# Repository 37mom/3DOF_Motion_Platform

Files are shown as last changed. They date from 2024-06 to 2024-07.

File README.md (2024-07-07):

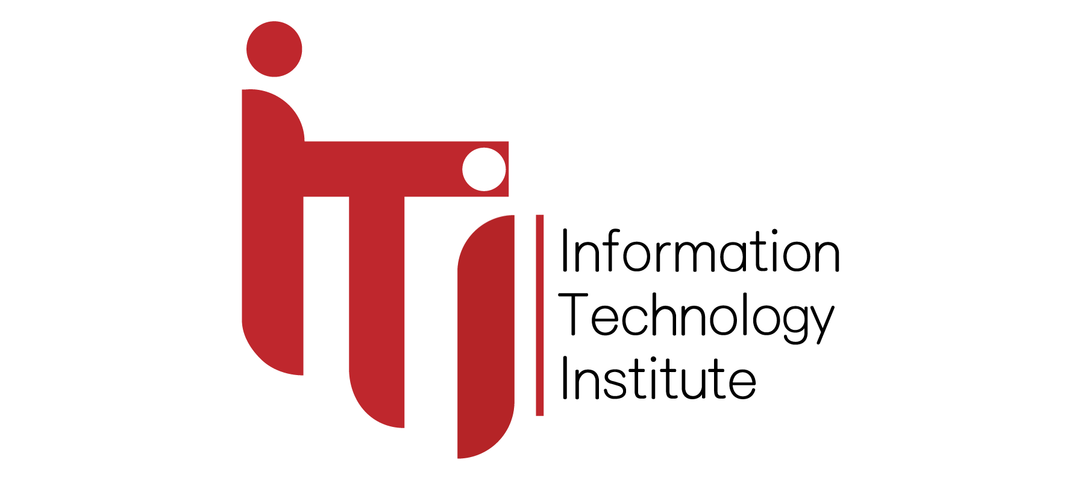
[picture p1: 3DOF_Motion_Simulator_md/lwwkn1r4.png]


> Information Technology Institute
>
> Motion Simulator
>
> Robotics
>
> Israa Ahmed Merhan Wael Mohamed Omar
>
> Submitted to Eng. Omar Shehata
>
> May 9, 2018
>
> Contents
>
> 1 Introduction 2
>
> 2 Robot Kinematics 3
>
> 3 Kinematics Of 3-DOF Parallel Robot 5 3.1 Forward Position Kinematics
> . . . . . . . . . . . . . . . . . . . 5 3.1.1 Vector loop equations: .
> . . . . . . . . . . . . . . . . . 5
>
> 3.1.2 Rotation Matrices . . . . . . . . . . . . . . . . . . . . . 5
> 3.1.3 EE Position Equations . . . . . . . . . . . . . . . . . . 8
> 3.1.4 Constrain Equations . . . . . . . . . . . . . . . . . . . 8
>
> 3.2 Solid-Work Model Veriﬁcation . . . . . . . . . . . . . . . . . . 9
> 3.3 Inverse Position Kinematics . . . . . . . . . . . . . . . . . . .
> 10 3.3.1 Orientation Equations . . . . . . . . . . . . . . . . . . 10
> 3.3.2 Passive angle equations . . . . . . . . . . . . . . . . . . 11
> 3.3.3 Position Equations . . . . . . . . . . . . . . . . . . . . 11
>
> 4 Forward Velocity Kinematics 12
>
> 5 Inverse Velocity Kinematics 13 5.1 Constrain equations
> diﬀerentiation . . . . . . . . . . . . . . . 13 5.2 EE position
> equations diﬀerentiation . . . . . . . . . . . . . . 13
>
> 6 Simulation 14 6.1 Trajectory Planning . . . . . . . . . . . . . . .
> . . . . . . . . 14 6.1.1 Circular Trajectory . . . . . . . . . . . . .
> . . . . . . . 15
>
> 6.1.2 Rectangular Trajectory . . . . . . . . . . . . . . . . . . 16
>
> 7 References 17
>
> 1

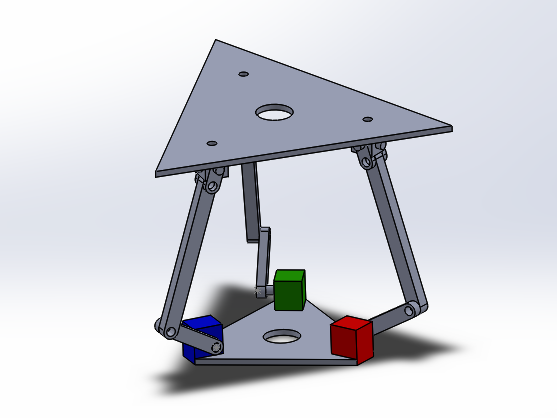
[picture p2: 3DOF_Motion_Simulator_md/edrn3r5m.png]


> 1 Introduction
>
> This project aims to design and manufacture a 3-DOF motion simulator
> plat-form. It is divided into three main parts : modelling, mechanical
> design and control.
>
> Motion simulators are used to simulate virtual motion into real life,
> for exam-ple they are used in ﬂight and car simulators to test
> aircrafts or cars or even to practice ﬂying an airplane before being
> in an actual one. Another usage of motion simulators which is the
> topic of this project is game simulation, for example imagine that you
> play a car-racing game while sitting on this platform you will
> experience the feeling of being inside the game.
>
> Figure 1: Solidworks model
>
> 2

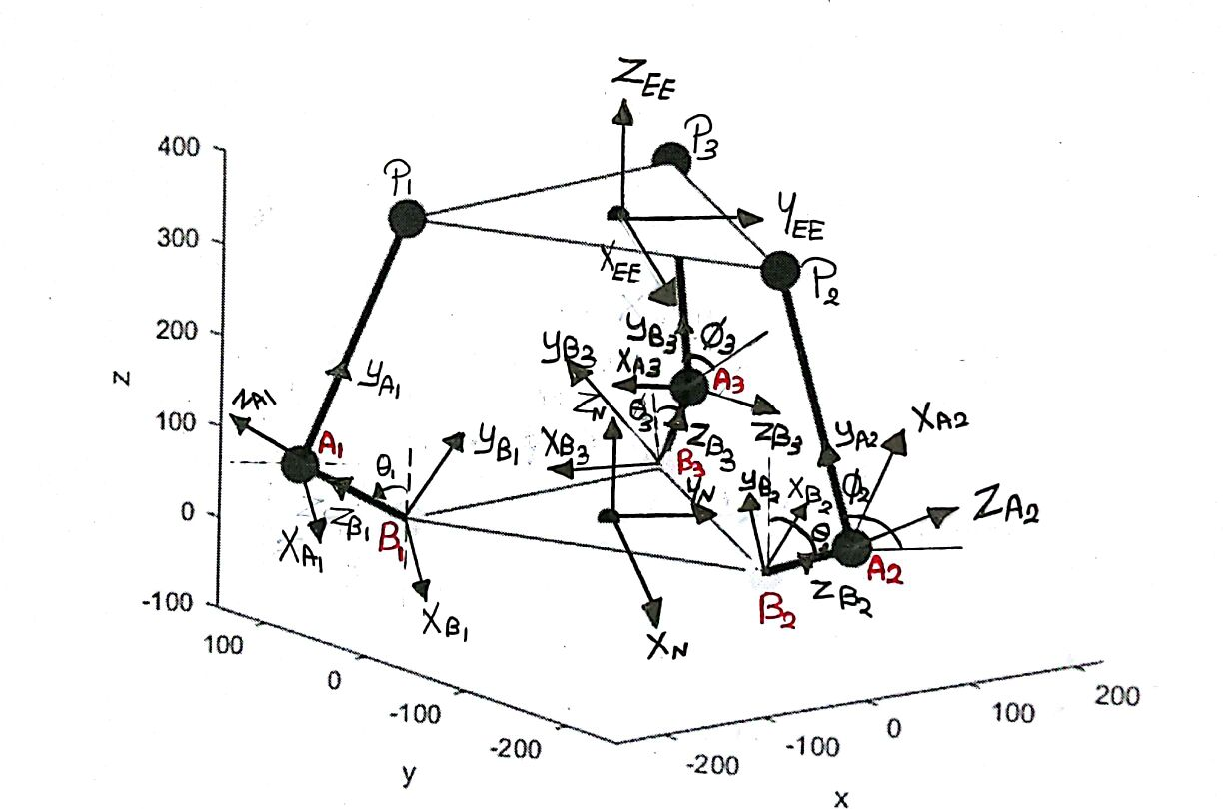
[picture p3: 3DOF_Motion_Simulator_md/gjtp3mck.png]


> 2 Robot Kinematics
>
> Our motion simulator can be described as a parallel manipulator with
> 3-DOF, two rotational motions (roll and pitch) and one translational
> motion in direction of Z-axis. The robot consists of 3 legs connected
> together through a platform, each leg consists of 2 links connected
> together through a revolute joint, each leg is connected to a motor
> through a revolute joint and to the platform through a U-joint.
>
> The kinematics problem of parallel manipulators is very tedious so we
> de-cided to simplify our problem by treating this robot as 3 serial
> robotic arms connected together through the platform which will be the
> work space of our robot, these ﬁxation points are ﬁxed in position
> forming an equilateral triangle and ﬁnally we neglected the presence
> of the U-joint but added the orientation of platform to our
> calculations. The motor axes of rotation are ﬁxed at 120 rotated from
> each other creating an equilateral triangle.
>
> Setting 2 coordinate systems for each link and the base frame. In the
> median of the base triangle the Newtonian frame XNYNZN is selected and
> this is the ﬁxed coordinate system. Z-axis in the ﬁxed frame is
> vertically
>
> 3
>
> upwards, X-axes of the frames at motor points are co-linear with the
> axes of rotation of the motors and the x-axis of the Newtonian frame
> is parallel to the axis of the ﬁrst coordinate system of the ﬁrst
> motor(B1). 0s are the 3 active angles of our system created by
> rotating about (Xi) and it is between the vertical axis of the base
> frame (ZN) and (ZBi) (ZB1 is coincident with
>
> the link BiAi) . is are the 3 passive angles created by rotating about
> (Xi) and they are measured between (YN) and (YAi) (YAi is coincident
> with the link AiPi).
>
> 4
>
> 3 Kinematics Of 3-DOF Parallel Robot
>
> 3.1 Forward Position Kinematics 3.1.1 Vector loop equations:
>
> Link(1):
>
> Link(2):
>
> Link(3):
>
> jrOE = -ljYN +l1jZB1 +l2jYA1 (1)

jrOE = ljXN + 2 l 3jYN +l1jZB2 +l2jYA2 (2)

> rOE = -ljXN + 2 l 3jYN +l1jZB3 +l2jYA3 (3)
>
> 3.1.2 Rotation Matrices
>
> Link(1):
>
> 2 1 0 NRB1 = 4 0 cos1
>
> 0 sin1

0 3 -sin1 5,

> cos1

2 1 0 NRA1 = 4 0 cos1

> 0 sin1

0 3 -sin1 5

> cos1
>
> 5
>
> Link(2):
>
> 2 cos -sin 0 3 NRB21 = 4 cos -sin 0 5,
>
> 0 0 1
>
> 1 0 0 A21RA2 = 4 0 cos2 -sin2 5,
>
> 0 sin2 cos2
>
> cos -cos2 sin sin2 sin NRB2 = sin cos2 cos -sin2 cos
>
> 1 0 0
>
> cos -cos2 sin sin2 sin NRA2 = sin cos2 cos -sin2 cos
>
> 1 0 0
>
> 2 1 0 B21RB2 = 4 0 cos2
>
> 0 sin2
>
> NRA21 = NRB21

3

5

> 3
>
> 5

0 3 -sin2 5

> cos2
>
> Link(3):
>
> 2 cos2 -sin2 0 3 NRB31 = 4 cos2 -sin2 0 5,
>
> 0 0 1
>
> 1 0 0 A31RA3 = 4 0 cos3 -sin3 5,
>
> 0 sin3 cos3
>
> cos2 -cos3 sin2 sin3 sin2 NRB3 = sin2 cos3 cos2 -sin3 cos2
>
> 1 0 0
>
> cos2 -cos3 sin2 sin3 sin2 NRA3 = sin2 cos3 cos2 -sin3 cos2
>
> 1 0 0
>
> 2 1 0 B31RB3 = 4 0 cos3
>
> 0 sin3
>
> NRA31 = NRB31

3

5

> 3
>
> 5

0 3 -sin3 5

> cos3
>
> 6
>
> Link 1: Where :
>
> ZB1 = -sin1jYN +cos1jZN (4) YA1 = cos1jYN +sin1jZN (5)
>
> Final Calculations:
>
> XP1 = 0
>
> YP1 = <u>-l</u> -l1 sin1 +l2 cos1
>
> ZP1 = l1 cos1 +l2 sin1
>
> Link 2: Where :
>
> ZB2 = sin sin2jXN -cos sin2jYN +cos2jZN (6) YA2 = sin sin2jXN
> -cossin2jYN +cos2jZN (7)
>
> Final Calculations:
>
> XP2 = <u>l</u> +l1 sin sin2 -l2 cos2 sin
>
> YP2 = 2 <u>l</u> 3 -l1 sin2 cos +l2 cos2 cos ZP2 = l1 cos2 +l2 sin2
>
> Link 3: Where :
>
> ZB3 = sin(2 )sin3jXN -cos(2 )sin3jYN +cos3jZN (8) YA3 = -sin(2
> )cos3jXN -cos(2 )cos3jYN +cos3jZN (9)
>
> 7
>
> Final Calculations:
>
> XP3 = <u>-l</u> +l1 sin(2 )sin3 -l2 cos3 sin(2 )
>
> YP3 = 2 <u>l</u> 3 -l1 sin3 cos(2 )+l2 cos3 cos(2 ) ZP2 = l1 cos3 +l2
> sin3
>
> 3.1.3 EE Position Equations
>
> The EE point is the median of the triangle connecting the 3-edges of
> the 3-Links.
>
> XEE = Xp1 +Xp2 +Xp3 (10)
>
> YEE = Yp1 +Yp2 +Yp3 (11)
>
> ZEE = Zp1 +Zp2 +Zp3 (12)
>
> 3.1.4 Constrain Equations
>
> The constrain Equation of this robot is that any distance between any
> two edges is constant and it is equal to the length of the triangle
> that connects the 3-edges.
>
> So the constrain equations are :
>
> ~~q~~
>
> C1 = (Xp1 -Xp2)2 +(Yp1 -Yp2)2 +(Zp1 -Zp2)2 (13)
>
> ~~q~~
>
> C2 = (Xp1 -Xp3)2 +(Yp1 -Yp3)2 +(Zp1 -Zp3)2 (14)
>
> ~~q~~
>
> C3 = (Xp3 -Xp2)2 +(Yp3 -Yp2)2 +(Zp3 -Zp2)2 (15)
>
> Where
>
> C1 = C2 = C3 = d (16)
>
> Where d is the length of the triangle.
>
> By solving the 3-previous equations using Newton Raphson , the passive
> angles 0s can be obtained.
>
> Applying 0s and 0s in the Vector Loop equations , the positions of the
> 3-edges and EE can be obtained.
>
> 8
>
> 3.2 Solid-Work Model Veriﬁcation
>
> Comparsion

||
||
||

||
||
||

||
||
||

||
||
||

82 76.63 82.8 80.63 77.47 83.746

||
||
||

||
||
||

||
||
||

88.86 88.86 88.69 90.85 90.85 90.85

||
||
||

||
||
||

||
||
||

68.244 68.244 68.244 69.98 69.98 69.98

||
||
||

||
||
||

||
||
||

69.45 84.32 74.63 69.76 85.73 75.78

||
||
||

> Table 1: Model Veriﬁcation
>
> 9
>
> 3.3 Inverse Position Kinematics 3.3.1 Orientation Equations
>
> Due to the platform orientation around x-axis and y-axis (Pitch and
> Roll) , the position of 3-edges of the triangle can be obtained as a
> function in the EE position and the platform orientation ( and ).
>
> is the angle due to the orientation around x-axis of the ﬁxed frame.
>
> is the angle due to the orientation around y-axis of the ﬁxed frame.
>
> 10
>
> 3.3.2 Passive angle equations
>
> Zpi = f(,) (17)
>
> The previous equation shows that 0s function in 0s and Zpi. So the
> equations will be:
>
> Link(1):
>
> Link(2):
>
> Link(3):

1 = sin-1(Zp1 -l1cos(1)) (18) 2

2 = sin-1(Zp2 -l1cos(2)) (19) 2

3 = sin-1(Zp3 -l1cos(3)) (20) 2

> 3.3.3 Position Equations
>
> -l -l1 sin1 +l2 cos1 -YP1 = 0 (21)
>
> 2 l 3 -l1 sin2 cos +l2 cos2 cos -YP2 = 0 (22) 2 l 3 -l1 sin3 cos(2
> )+l2 cos3 cos(2 )-YP3 = 0 (23)
>
> by substituting equations 18,19,20 in equations 21,22,23 ,we can get
> the 0s and 0s.
>
> 11
>
> 4 Forward Velocity Kinematics
>
> In order to solve the velocity kinematics problem, the velocity of the
> end eﬀector must be found using the angular speed of the motors as the
> input. After diﬀerentiating the constraint equations using the
> following equations :
>
> @C1 @C1 @i @C1 @i @t @i @t @i @t
>
> @C2 @C2 @i @C2 @i @t @i @t @i @t @C3 @C3 @i @C3 @i
>
> @t @i @t @i @t

\(24\)

\(25\)

\(26\)

> Now these equations become 3 linear equations in 0s (passive angles’
> angular velocities) because in these equations the end eﬀector
> position, mo-tor angles and passive angles are givens to these
> equations , by solving them together we obtain 0s . Now it’s necessary
> to diﬀerentiate the end eﬀector position equations for each link in
> order to obtain the velocity of the end eﬀector of the whole platform.
>
> As,
>
> XEE = Xp1 +Xp2 +Xp3 (27)
>
> YEE = Yp1 +Yp2 +Yp3 (28)
>
> ZEE = Zp1 +Zp2 +Zp3 (29)
>
> 12
>
> 5 Inverse Velocity Kinematics
>
> The inverse velocity kinematic problem can be solved by getting the
> values of angular velocity (i).
>
> By diﬀerentiating the EE position equations and the constrain
> equations w.r.t and .
>
> 5.1 Constrain equations diﬀerentiation
>
> @C1 @C1 @i @C1 @i @t @i @t @i @t @C2 @C2 @i @C2 @i @t @i @t @i @t @C3
> @C3 @i @C3 @i @t @i @t @i @t
>
> 5.2 EE position equations diﬀerentiation

\(30\)

\(31\)

\(32\)

> @XEE 1 @(Xp1 +Xp2 +Xp3)@i @(Xp1 +Xp2 +Xp3)@i @t 3 @i @t @i @t
>
> @YEE 1 @(Yp1 +Yp2 +Yp3)@i @(Yp1 +Yp2 +Yp3)@i @t 3 @i @t @i @t
>
> @ZEE 1 @(Zp1 +Zp2 +Zp3)@i @(Zp1 +Zp2 +Zp3)@i @t 3 @i @t @i @t

\(33\)

\(34\)

\(35\)

> Where XEE , YEE and ZEE are the input to the inverse velocity
> kinematic problem . So, by solving this 6-equations using fsolve
> function , i and i can be obtained.
>
> 13
>
> 6 Simulation
>
> 6.1 Trajectory Planning
>
> In this section it is supposed to simulate the motion of a ball on the
> plat-form using the robot kinematics. In order to simulate the ball
> motion, the diﬀerential equations describing the ball motion is added
> to the rest of the system’s equation.
>
> a1 dtx + dt a2 +a3 dt+xdt 2 = -gsin (36)
>
> 2 2
>
> a1 dt2 + dt a2 +a3 dt +y dt = -gsin (37)
>
> As,
>
> a1 = 1+ mb(rb)2 a2 = mbrb
>
> Where,

a3 = Kcx b

> mb is the ball mass.
>
> rb is the ball radius.
>
> Jb is the moment of inertia of the ball.
>
> Kb is the coeﬃcient of friction of the ball.
>
> By changing the orientation of the platform (by changing values of & )
> with respect to time in order to set a rectangular and a circular
> trajectories for the ball then solving the previous equations for
> these inputs to specify the position of the ball on the plate.
>
> 14

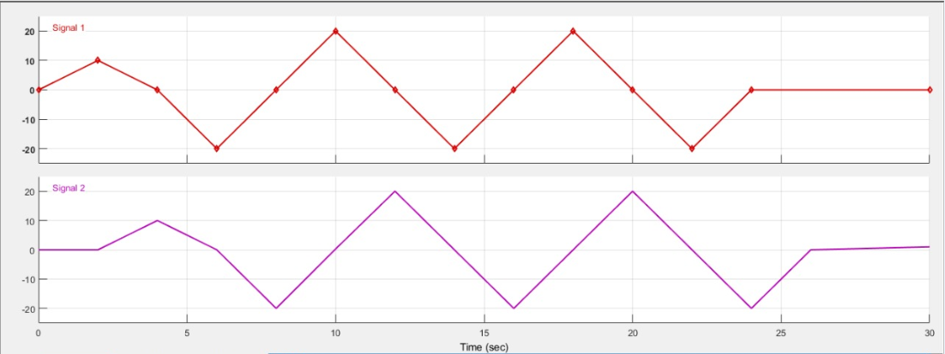
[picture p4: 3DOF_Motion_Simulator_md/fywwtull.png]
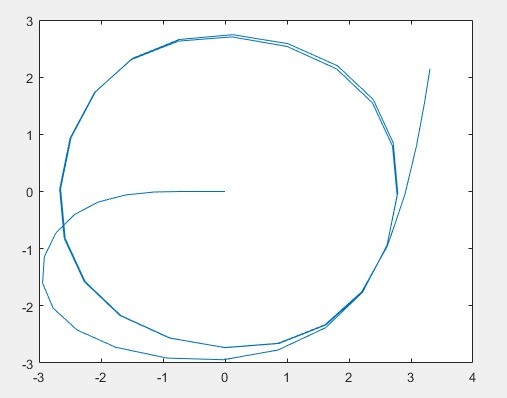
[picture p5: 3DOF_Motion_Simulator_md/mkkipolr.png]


> 6.1.1 Circular Trajectory
>
> System Input Signal:
>
> Figure 2: Orientation angles input
>
> Path:
>
> Figure 3: Circular trajectory
>
> 15

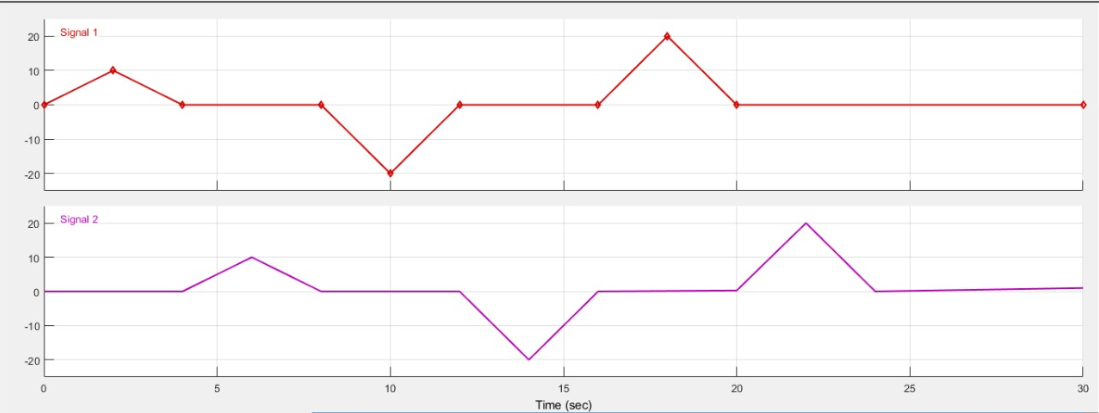
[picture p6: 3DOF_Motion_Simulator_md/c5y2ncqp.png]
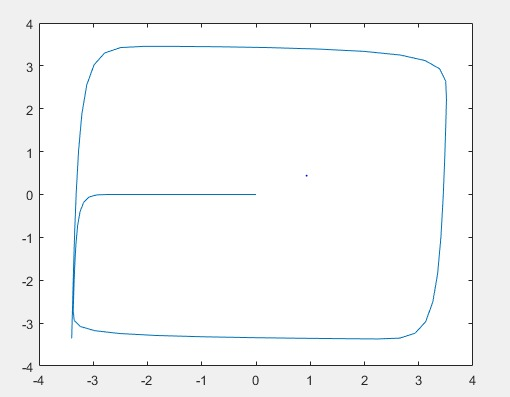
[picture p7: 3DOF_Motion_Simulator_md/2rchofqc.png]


> 6.1.2 Rectangular Trajectory
>
> System Input Signal:
>
> Figure 4: Orientation angles input
>
> Path:
>
> Figure 5: Rectangle trajectory
>
> 16
>
> 7 References
>
> 1\. An Upper Limb Rehabilitation Robot Based on 3-RRC Parallel
> Mech-anism Hongbo Wang, Ning Du, Huina Hou, Jiangshun Zhao and
> Hong-nian Yu,Proceedings of the 2012 International Conference on
> Advanced Mechatronic Systems, Tokyo, Japan, September 18-21,2012.
>
> 2\. Kinematics and dynamics analysis of a three degree-of-freedom
> paral-lel manipulator LIU Shan-zeng, ZHU Zhen-cai, SUN Zhao-peng, CAO
> Guo-hua School of Mechanical and Electrical Engineering, China
> Uni-versity of Mining and Technology, Xuzhou 221116, China Central
> South University Press and Springer-Verlag Berlin Heidelberg 2014,J.
> Cent. South Univ. (2014).
>
> 3\. Modelling of Ball and Plate System Based on First Principle Model
> and Optimal Control František Dušek, Daniel Honc, Rahul Sharma K.
> Department of Process Control, Faculty of Electrical Engineering and
> Informatics University of Pardubice nám. Čs. legií 565, 532 10
> Par-dubice, Czech Republic frantisek.dusek@upce.cz,
> daniel.honc@upce.cz, rahul.sharma@student.upce.cz, 2017 21st
> International Conference on Process Control (PC) June 6–9, 2017,
> Štrbské Pleso, Slovakia.
>
> 17

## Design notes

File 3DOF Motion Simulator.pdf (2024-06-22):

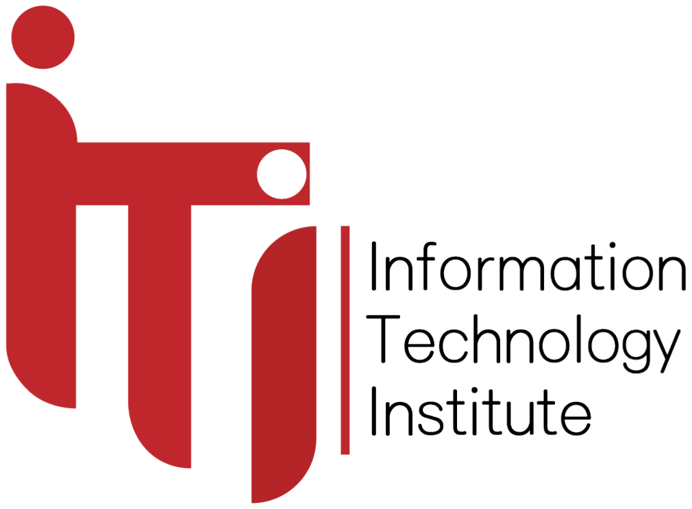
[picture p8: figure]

Information Technology Institute

Motion Simulator

# Robotics

## Israa Ahmed Merhan Wael Mohamed Omar

Submitted to
Eng. Omar Shehata

### May 9, 2018

## Contents

1 Introduction | 2
2 Robot Kinematics | 3
3 Kinematics Of 3-DOF Parallel Robot | 5
4 Forward Velocity Kinematics | 12
5 Inverse Velocity Kinematics | 13
6 Simulation | 14
7 References | 17

1

## 1 Introduction

This project aims to design and manufacture a 3-DOF motion simulator platform. It is divided into three main parts : modelling, mechanical design and control.
Motion simulators are used to simulate virtual motion into real life, for example they are used in flight and car simulators to test aircrafts or cars or even to practice flying an airplane before being in an actual one. Another usage of motion simulators which is the topic of this project is game simulation, for example imagine that you play a car-racing game while sitting on this platform you will experience the feeling of being inside the game.

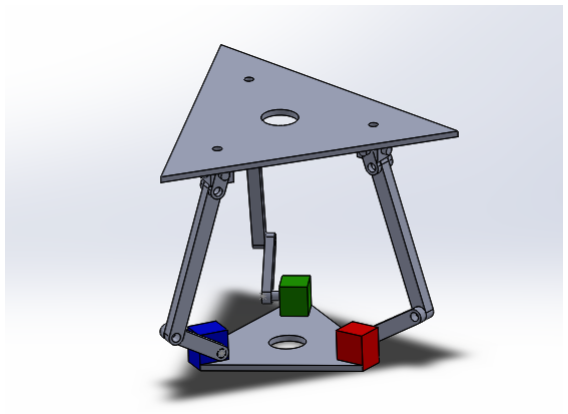
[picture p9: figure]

Figure 1: Solidworks model

2

## 2 Robot Kinematics

Our motion simulator can be described as a parallel manipulator with 3-DOF, two rotational motions (roll and pitch) and one translational motion in direction of Z-axis. The robot consists of 3 legs connected together through a platform, each leg consists of 2 links connected together through a revolute joint, each leg is connected to a motor through a revolute joint and to the platform through a U-joint.

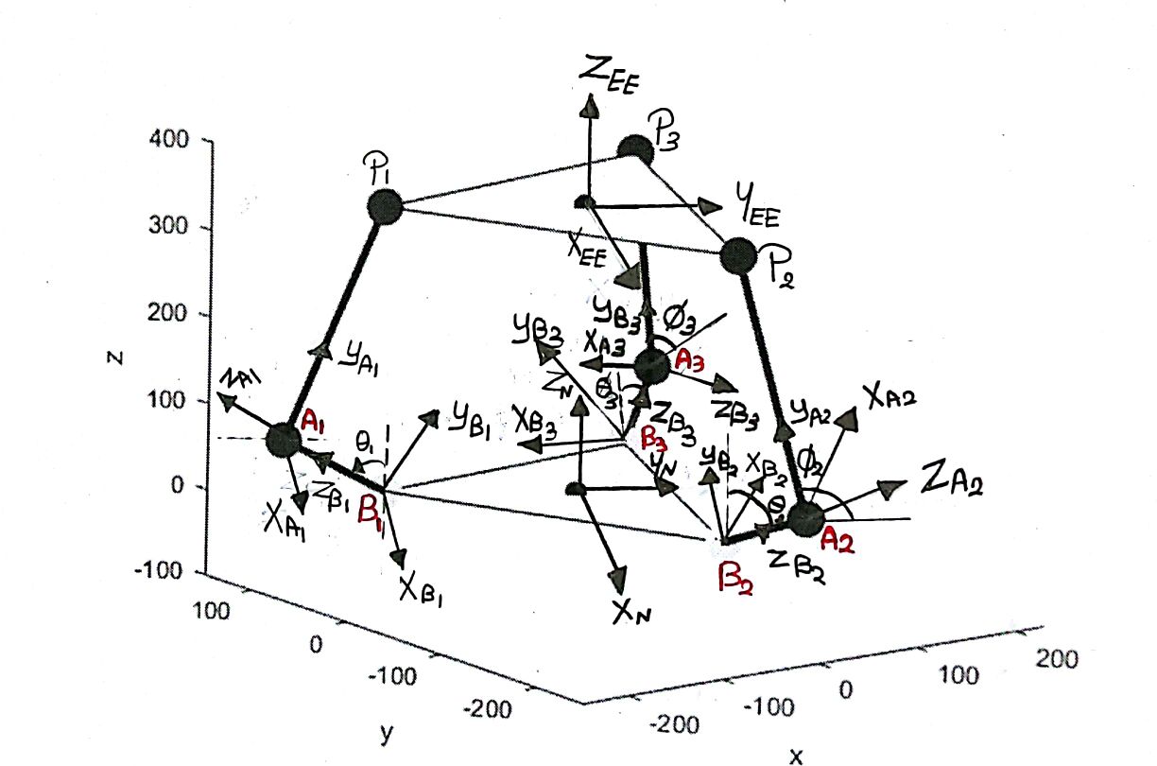
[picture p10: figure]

The kinematics problem of parallel manipulators is very tedious so we de-cided to simplify our problem by treating this robot as 3 serial robotic arms connected together through the platform which will be the work space of our robot, these fixation points are fixed in position forming an equilateral triangle and finally we neglected the presence of the U-joint but added the orientation of platform to our calculations. The motor axes of rotation are fixed at 120◦
rotated from each other creating an equilateral triangle.

Setting 2 coordinate systems for each link and the base frame. In the median of the base triangle the Newtonian frame XNYNZN is selected and this is the fixed coordinate system. Z-axis in the fixed frame is vertically

3

upwards, X-axes of the frames at motor points are co-linear with the axes of rotation of the motors and the x-axis of the Newtonian frame is parallel to the axis of the first coordinate system of the first motor(B1). θ

0
i

s are the 3
active angles of our system created by rotating about (Xi) and it is between the vertical axis of the base frame (ZN) and (ZBi

) (ZB1
is coincident with
the link BiAi) . φ⁰
i

s are the 3 passive angles created by rotating about (Xi) and they are measured between (YN) and (YAi

) (YAi
is coincident with the
link AiPi).

4

## 3 Kinematics Of 3-DOF Parallel Robot

### 3.1 Forward Position Kinematics

### 3.1.1 Vector loop equations:

- Link(1):

|r

OE =

−l
√
3
|YN + l1|ZB1 + l2|YA1 | (1)
- Link(2):

|r

OE =

l
2

|XN +

l
2

√
3
|YN + l1|ZB2 + l2|YA2 | (2)
- Link(3):

r

OE =

−l
√
3

|XN +

l
2

√
3
|YN + l1|ZB3 + l2|YA3 | (3)

### 3.1.2 Rotation Matrices

- Link(1):

NRB1 =

1 | 0 | 0
0 cos θ1 | − sin θ1
0 sin θ1 | cos θ1
- ,

NRA1 =

1 | 0 | 0
0 cos φ1 | − sin φ1
0 sin φ1 | cos φ1

5

- Link(2):

NRB21 =

cos ψ − sin ψ 0
cos ψ − sin ψ 0
0 | 0 | 1
- ,

B21 RB2 =

1 | 0 | 0
0 cos θ2 | − sin θ2
0 sin θ2 | cos θ2

A21 RA2 =

1 | 0 | 0
0 cos φ2 | − sin φ2
0 sin φ2 | cos φ2
- ,

NRA21 =
NRB21

NRB2 =

cos ψ − cos θ2 sin ψ | sin θ2 sin ψ
sin ψ | cos θ2 cos ψ | − sin θ2 cos ψ
1 | 0 | 0

NRA2 =

cos ψ − cos φ2 sin ψ | sin φ2 sin ψ
sin ψ | cos φ2 cos ψ | − sin φ2 cos ψ
1 | 0 | 0
- Link(3):

NRB31 =

cos 2ψ − sin 2ψ 0
cos 2ψ − sin 2ψ 0
0 | 0 | 1
- ,

B31 RB3 =

1 | 0 | 0
0 cos θ3 | − sin θ3
0 sin θ3 | cos θ3

A31 RA3 =

1 | 0 | 0
0 cos φ3 | − sin φ3
0 sin φ3 | cos φ3
- ,

NRA31 =

NRB31

NRB3 =

cos 2ψ − cos θ3 sin 2ψ | sin θ3 sin 2ψ
sin 2ψ | cos θ3 cos 2ψ | − sin θ3 cos 2ψ
1 | 0 | 0

NRA3 =

cos 2ψ − cos φ3 sin 2ψ | sin φ3 sin 2ψ
sin 2ψ | cos φ3 cos 2ψ | − sin φ3 cos 2ψ
1 | 0 | 0

6

- Link 1:

Where :

ZB1 = − sin θ1|YN + cos θ1|ZN | (4)
YA1 = cos φ1|YN + sin φ1|ZN | (5)

Final Calculations:

- XP1 = 0
- YP1 = √⁻l
3

− l1 sin θ1 + l2 cos φ1

- ZP1 = l1 cos θ1 + l2 sin φ1
- Link 2:

Where :

ZB2 = sin ψ sin θ2|XN − cos ψ sin θ2|YN + cos θ2|ZN | (6)
YA2 = sin ψ sin φ2|XN − cos sin φ2|YN + cos φ2|ZN | (7)

Final Calculations:

- XP2 =

l
2 + l1 sin ψ sin θ2 − l2 cos φ2 sin ψ
- YP2 =

l
2

√
3

− l1 sin θ2 cos ψ + l2 cos φ2 cos ψ

- ZP2 = l1 cos θ2 + l2 sin φ2
- Link 3:

Where :

ZB3 = sin(2ψ)sin θ3|XN − cos(2ψ)sin θ3|YN + cos θ3|ZN | (8)
YA3 = − sin(2ψ) cos φ3|XN − cos(2ψ) cos φ3|YN + cos φ3|ZN | (9)

7

Final Calculations:

- XP3 = √⁻l
3

+ l1 sin(2ψ)sin θ3 − l2 cos φ3 sin(2ψ)

- YP3 =

l
2

√
3

− l1 sin θ3 cos(2ψ) + l2 cos φ3 cos(2ψ)

- ZP2 = l1 cos θ3 + l2 sin φ3

### 3.1.3 EE Position Equations

- The EE point is the median of the triangle connecting the 3-edges of the 3-Links.

XEE =

Xp1 + Xp2 + Xp3
3

(10)

YEE =

Yp1 + Yp2 + Yp3
3

(11)

ZEE =

Zp1 + Zp2 + Zp3
3

(12)

### 3.1.4 Constrain Equations

The constrain Equation of this robot is that any distance between any two edges is constant and it is equal to the length of the triangle that connects the 3-edges.
So the constrain equations are :

C1 =

q
(Xp1 − Xp2)

2 + (Yp1 − Yp2)

2 + (Zp1 − Zp2)

2

(13)

C2 =

q
(Xp1 − Xp3)

2 + (Yp1 − Yp3)

2 + (Zp1 − Zp3)

2

(14)

C3 =

q
(Xp3 − Xp2)

2 + (Yp3 − Yp2)

2 + (Zp3 − Zp2)

2

(15)

Where
C1 = C2 = C3 = d | (16)

Where d is the length of the triangle.
By solving the 3-previous equations using Newton Raphson , the passive angles φ⁰
s can be obtained.
Applying θ

0

s and φ⁰
s in the Vector Loop equations , the positions of the 3-edges and EE can be obtained.

8

### 3.2 Solid-Work Model Verification

Comparsion | Solid-Work Result | Matlab Results
φ1 | φ2 | φ3 | φ1 | φ2 | φ3
θ1 | 30◦
82◦ | 76.63◦ | 82.8◦ | 80.63◦ | 77.47◦ | 83.746◦
θ2 | 40◦
θ3 | 20◦
θ1 | 0

◦
88.86◦ | 88.86◦ | 88.69◦ | 90.85◦ | 90.85◦ | 90.85◦
θ2 | 0

◦

θ3 0

◦

θ1 | 90◦
68.244◦ | 68.244◦ | 68.244◦ | 69.98◦ | 69.98◦ | 69.98◦
θ2 | 90◦
θ3 | 90◦
θ1 | 70◦
69.45◦ | 84.32◦ | 74.63◦ | 69.76◦ | 85.73◦ | 75.78◦
θ2 | 10◦
θ3 | 50◦

Table 1: Model Verification

9

### 3.3 Inverse Position Kinematics

### 3.3.1 Orientation Equations

- Due to the platform orientation around x-axis and y-axis (Pitch and Roll) , the position of 3-edges of the triangle can be obtained as a function in the EE position and the platform orientation (α and β).
- α is the angle due to the orientation around x-axis of the fixed frame.
- β is the angle due to the orientation around y-axis of the fixed frame.

Link(1):

- XP1 = 0
- YP1 = YEE −

dcos(α)
√
3
- ZP1 = ZEE +

d
2

sin(β)+sin(α)
√
3

Link(2):

- XP2 = XEE +

d
2

cos(β)

- YP2 =

−Yp2
2 −

3YEE
2
- ZP2 = ZEE +

d
2

−sin(β)+sin(α)
√
3

Link(3):

- XP3 = XEE −

d
2

cos(β)

- YP3 = Yp2
- ZP3 = ZEE + d

sin(α)
√
3

10

### 3.3.2 Passive angle equations

Zpi = f(θ, φ) | (17)

The previous equation shows that φ⁰ s function in θ

0
s and Zpi.
So the equations will be:
- Link(1):

φ1 = sin⁻¹
(

Zp1 − l1cos(θ1)
l2
) | (18)
- Link(2):

φ2 = sin⁻¹
(

Zp2 − l1cos(θ2)
l2
) | (19)
- Link(3):

φ3 = sin⁻¹
(

Zp3 − l1cos(θ3)
l2
) | (20)

### 3.3.3 Position Equations

−l
√
3
− l1 sin θ1 + l2 cos φ1 − YP1 = 0 | (21)

l
2

√
3
− l1 sin θ2 cos ψ + l2 cos φ2 cos ψ − YP2 = 0 | (22)

l
2

√
3
− l1 sin θ3 cos(2ψ) + l2 cos φ3 cos(2ψ) − YP3 = 0 | (23)

by substituting equations 18,19,20 in equations 21,22,23 ,we can get the θ

0
s
and φ⁰
s.

11

## 4 Forward Velocity Kinematics

In order to solve the velocity kinematics problem, the velocity of the end effector must be found using the angular speed of the motors as the input. After differentiating the constraint equations using the following equations :

∂C1
∂t =

∂C1
∂θi

∂θi
∂t +

∂C1
∂φi

∂φi
∂t | (24)

∂C2
∂t =

∂C2
∂θi

∂θi
∂t +

∂C2
∂φi

∂φi
∂t | (25)

∂C3
∂t =

∂C3
∂θi

∂θi
∂t +

∂C3
∂φi

∂φi
∂t | (26)
Now these equations become 3 linear equations in φ˙ 0 | s (passive angles’
angular velocities) because in these equations the end effector position, motor angles and passive angles are givens to these equations , by solving them together we obtain φ˙ 0
s . Now it’s necessary to differentiate the end effector position equations for each link in order to obtain the velocity of the end effector of the whole platform.
As,

X˙
EE =

X˙

p1 + X˙

p2 + X˙
p3
3

(27)

Y˙
EE =

Y˙

p1 + Y˙

p2 + Y˙
p3
3

(28)

Z˙
EE =

Z˙

p1 + Z˙

p2 + Z˙
p3
3

(29)

12

## 5 Inverse Velocity Kinematics

The inverse velocity kinematic problem can be solved by getting the values of angular velocity (θ˙
i).
By differentiating the EE position equations and the constrain equations w.r.t θ and φ.

### 5.1 Constrain equations differentiation

∂C1
∂t =

∂C1
∂θi

∂θi
∂t +

∂C1
∂φi

∂φi
∂t | (30)

∂C2
∂t =

∂C2
∂θi

∂θi
∂t +

∂C2
∂φi

∂φi
∂t | (31)

∂C3
∂t =

∂C3
∂θi

∂θi
∂t +

∂C3
∂φi

∂φi
∂t | (32)

### 5.2 EE position equations differentiation

∂XEE
∂t =

1
3

(

∂(Xp1 + Xp2 + Xp3)
∂θi

∂θi

∂t + (∂(Xp1 + Xp2 + Xp3)
∂φi

∂φi
∂t ) (33)

∂YEE
∂t =

1
3

(

∂(Yp1 + Yp2 + Yp3)
∂θi

∂θi

∂t + (∂(Yp1 + Yp2 + Yp3)
∂φi

∂φi
∂t ) (34)

∂ZEE
∂t =

1
3

(

∂(Zp1 + Zp2 + Zp3)
∂θi

∂θi

∂t + (∂(Zp1 + Zp2 + Zp3)
∂φi

∂φi
∂t ) (35)

Where X˙

EE , Y˙

EE and Z˙
EE are the input to the inverse velocity kinematic problem . So, by solving this 6-equations using fsolve function , θ˙

i and φ˙
| i
can be obtained.

13

## 6 Simulation

### 6.1 Trajectory Planning

In this section it is supposed to simulate the motion of a ball on the platform using the robot kinematics. In order to simulate the ball motion, the differential equations describing the ball motion is added to the rest of the system’s equation.

a1

d

2x
dt²

+

dx

dt
a2 + a3

dx
dt
+ x
dβ

dt 2
= −g sin β | (36)

a1

d

2y
dt²

+

dy

dt
a2 + a3

dy
dt
+ y
dα

dt 2
= −g sin α | (37)

As,

a1 = 1 +

Jb
mb(rb)

2

a2 =

Kb
mbrb

a3 =

Kcx
mb

Where,

- mb is the ball mass.
- rb is the ball radius.
- Jb is the moment of inertia of the ball.
- Kb is the coefficient of friction of the ball.

By changing the orientation of the platform (by changing values of α&β ) with respect to time in order to set a rectangular and a circular trajectories for the ball then solving the previous equations for these inputs to specify the position of the ball on the plate.

14

### 6.1.1 Circular Trajectory

System Input Signal:


Figure 2: Orientation angles input

Path:

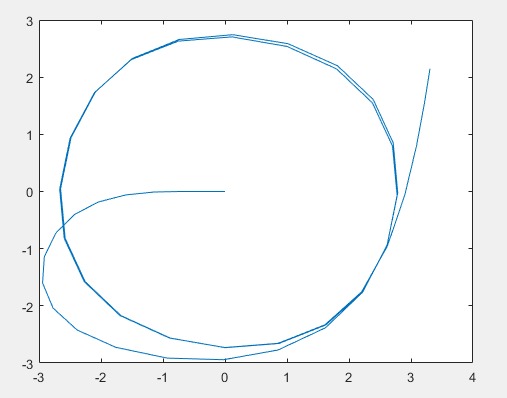
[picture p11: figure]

Figure 3: Circular trajectory

15

### 6.1.2 Rectangular Trajectory

System Input Signal:


Figure 4: Orientation angles input

Path:

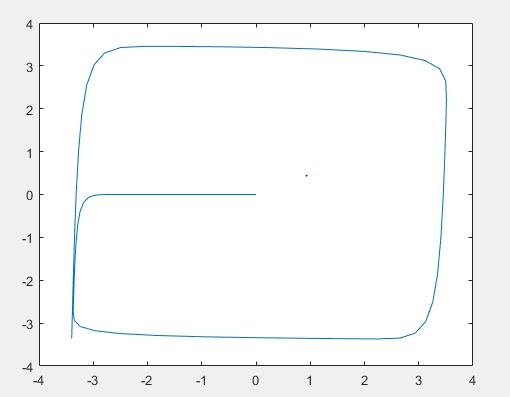
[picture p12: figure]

Figure 5: Rectangle trajectory

16

## 7 References

1. An Upper Limb Rehabilitation Robot Based on 3-RRC Parallel Mech-anism Hongbo Wang, Ning Du, Huina Hou, Jiangshun Zhao and Hong-nian Yu,Proceedings of the 2012 International Conference on Advanced Mechatronic Systems, Tokyo, Japan, September 18-21,2012.
2. Kinematics and dynamics analysis of a three degree-of-freedom parallel manipulator LIU Shan-zeng, ZHU Zhen-cai, SUN Zhao-peng, CAO Guo-hua School of Mechanical and Electrical Engineering, China University of Mining and Technology, Xuzhou 221116, China Central South University Press and Springer-Verlag Berlin Heidelberg 2014,J. Cent. South Univ. (2014).
3. Modelling of Ball and Plate System Based on First Principle Model and Optimal Control František Dušek, Daniel Honc, Rahul Sharma K. Department of Process Control, Faculty of Electrical Engineering and Informatics University of Pardubice nám. Čs. legií 565, 532 10 Pardubice, Czech Republic frantisek.dusek@upce.cz, daniel.honc@upce.cz, rahul.sharma@student.upce.cz, 2017 21st International Conference on Process Control (PC) June 6–9, 2017, Štrbské Pleso, Slovakia.

17

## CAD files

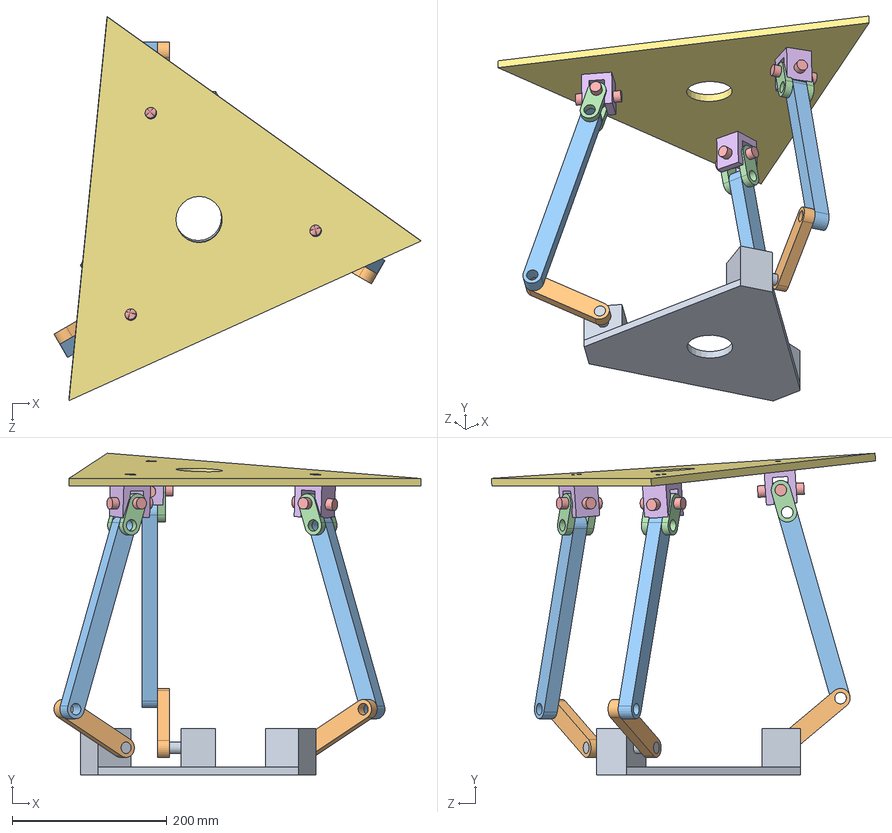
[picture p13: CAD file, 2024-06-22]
Mechanical Design/Sketch/motion simulator/ass1.SLDASM
474.9 x 416.2 x 497.2 mm
base
link1 x 3
link2 x 3
conn x 6
plus x 3
u x 3
plate

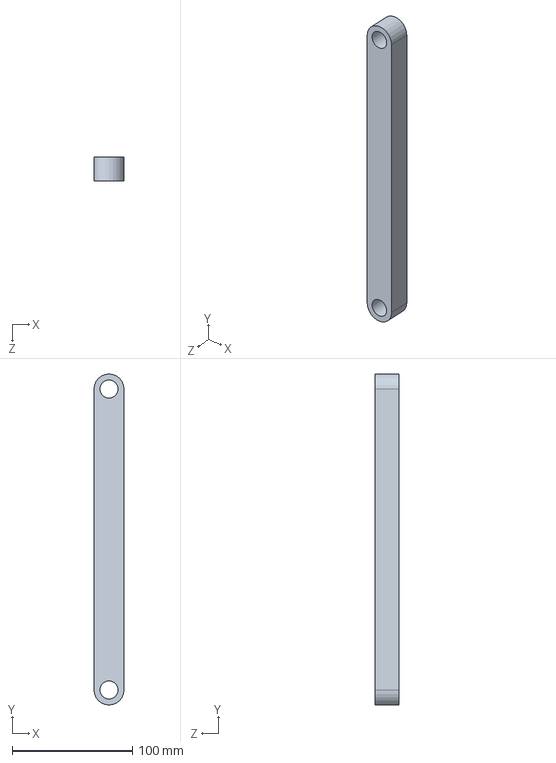
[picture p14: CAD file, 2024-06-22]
Mechanical Design/Sketch/motion simulator/link2.SLDPRT
25.0 x 275.0 x 20.0 mm

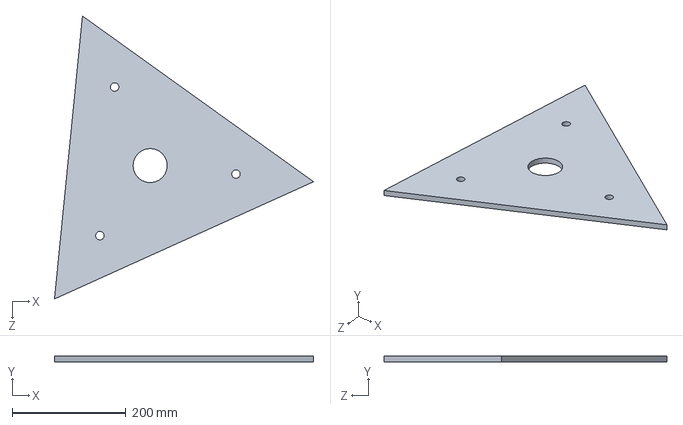
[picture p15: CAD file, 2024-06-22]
Mechanical Design/Sketch/motion simulator/plate.SLDPRT
455.5 x 10.0 x 497.6 mm

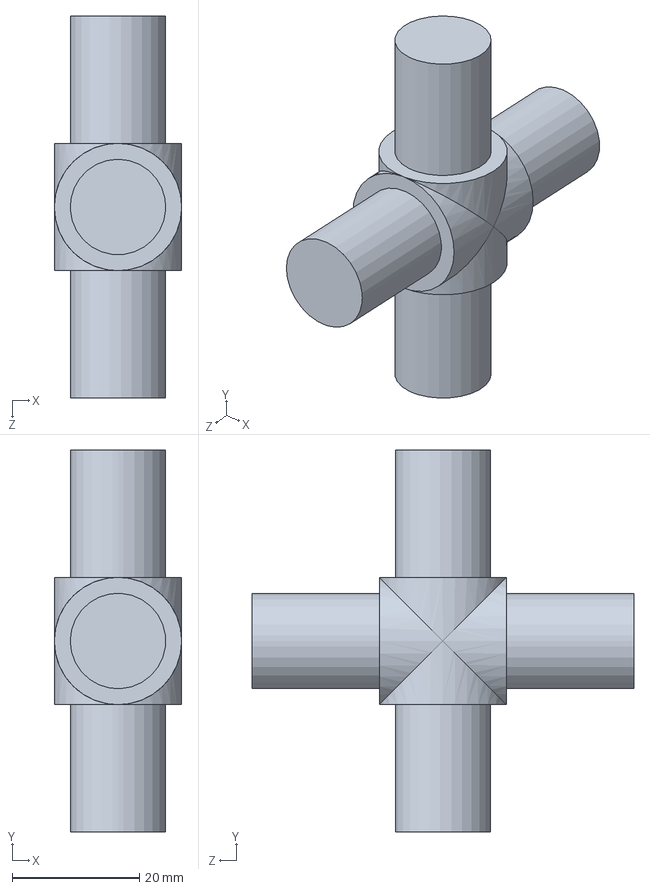
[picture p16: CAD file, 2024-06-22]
Mechanical Design/Sketch/motion simulator/plus.SLDPRT
20.0 x 60.0 x 60.0 mm

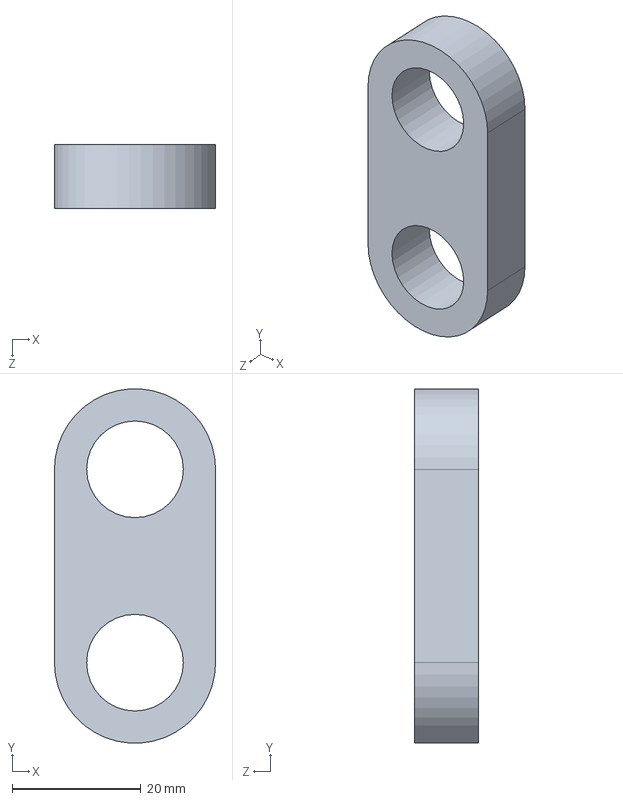
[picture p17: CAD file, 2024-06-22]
Mechanical Design/Sketch/motion simulator/conn.SLDPRT
25.0 x 54.9 x 10.0 mm

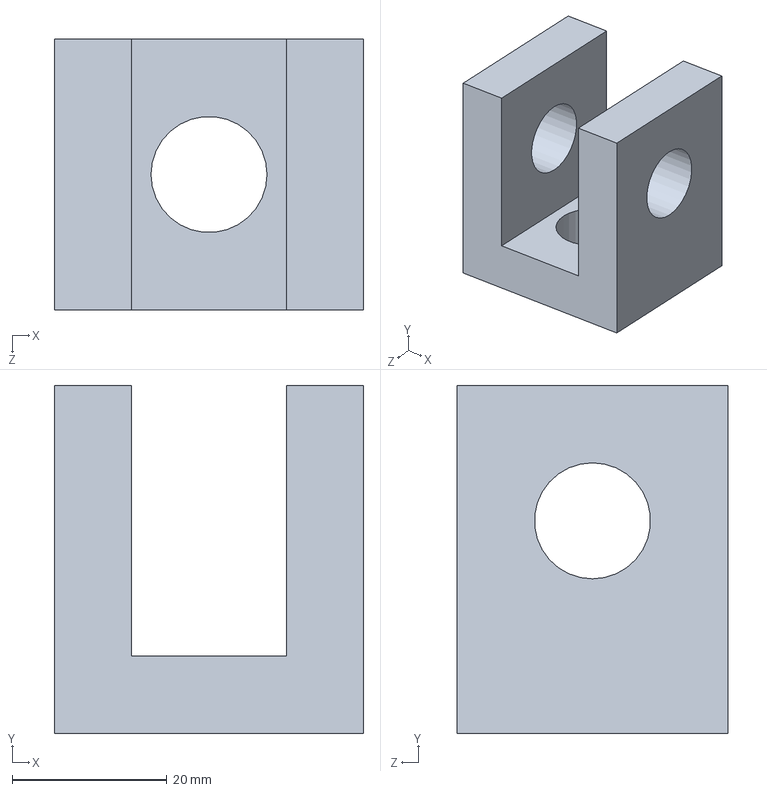
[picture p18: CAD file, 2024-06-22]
Mechanical Design/Sketch/motion simulator/u.SLDPRT
40.0 x 45.0 x 35.0 mm

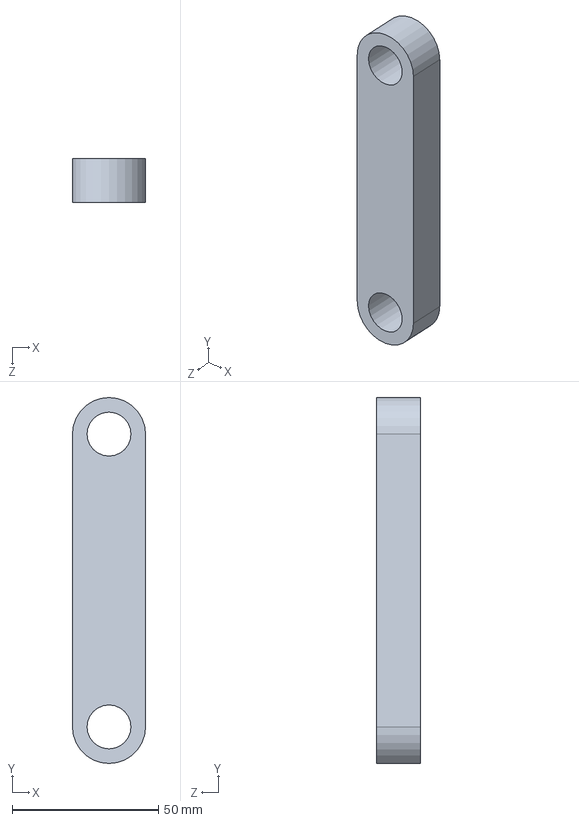
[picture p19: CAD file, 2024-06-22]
Mechanical Design/Sketch/motion simulator/link1.SLDPRT
25.0 x 125.0 x 15.0 mm

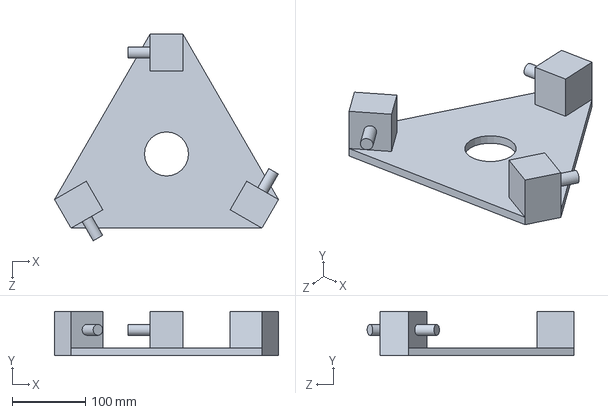
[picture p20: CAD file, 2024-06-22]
Mechanical Design/Sketch/motion simulator/base.SLDPRT
305.0 x 60.0 x 281.4 mm

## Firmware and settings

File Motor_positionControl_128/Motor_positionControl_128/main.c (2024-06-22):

/*
 * Motor_positionControl_128.c
 *
 * Created: 6/20/2018 12:16:07 AM
 * Author : moham
 */ 

#ifdef F_CPU
#undef F_CPU
#define F_CPU 8000000UL
#endif

#ifndef F_CPU
#define F_CPU 8000000UL
#endif

#include <avr/io.h>
#include <util/atomic.h> 
#include "util/delay.h"
#include <avr/interrupt.h>
#include "Timers.h"
#include "motorController.h"
#include "ADC.h"
#include "USART_128.h"
#include "data_types.h"
#include "pid.h"


#define loopTIME						10000	//10ms
#define Hz								100
#define CHANNEL_NUM						 0

PID_t position_pid[3] ={0};

float dt = 0;

float filter[2]={0};
float filter2[2]={0};
float filter3[2]={0};
	
uint32_t ADC_accu[3] = {0} ;
float       Angle[3] = {0} ;
int       PWMDuty[3] = {0} ;
uint16_t  counter[3] = {0} ;
float    setPoint[3] = {0};
uint8_t  UarTemp=0 ;

char buffer[20];

void LPfilter(float rawDATA, float *filteredARRAY, float LPFgain);
float calc_Angle(float ADC_value);
void receiveAngles(char *str,float *receivedSetPoints);
void cleanArr(char* StringPtr);



int main(void)
{
	float kp=  5  ;    float kp2=  5  ;	 float  kp3 =  5  ;    
	float ki = 0.0  ;  float ki2 = 0.0  ; float ki3 = 0.0  ;
	float kd = 0.031 ; float kd2 = 0.031 ;float kd3 = 0.031 ;
	
	init_loop_timer() ;
	int_PWM_timers() ;
	init_MotorController();
	ADC_init();
	USART_init(0);
	sei(); // Enable Global interrupts
	
	pid_init(&position_pid[0],kp,ki,kd);
	pid_set(&position_pid[0] ,setPoint[0]);
	
	pid_init(&position_pid[1],kp2,ki2,kd2);
	pid_set(&position_pid[1] ,setPoint[1]);
	
	pid_init(&position_pid[2],kp3,ki3,kd3);
	pid_set(&position_pid[2],setPoint[2]);
	_delay_ms(2000);
	
	setPoint[0]=  Angle[0];
	setPoint[1]=  Angle[1];
	setPoint[2]=  Angle[2];
	while (1)
	{
		
		if (TCNT1>=loopTIME)
		{
			dt = (float)TCNT1/1000000;
			TCNT1 = 0;
			
			PWMDuty[0] =pid_calculate(&position_pid[0],(int)Angle[0]-setPoint[0],dt);
			PWMDuty[1] =pid_calculate(&position_pid[1],(int)Angle[1]-setPoint[1],dt);
			PWMDuty[2] =pid_calculate(&position_pid[2],(int)Angle[2]-setPoint[2],dt);
			driveMotor(PWMDuty[0],PWMDuty[1],PWMDuty[2]);
			
			pid_set(&position_pid[0] ,0);
			pid_set(&position_pid[1], 0);
			pid_set(&position_pid[2] ,0);
		}
	}
}




void LPfilter(float rawDATA, float *filteredARRAY, float LPFgain)
{
	filteredARRAY[0] = rawDATA*LPFgain + filteredARRAY[1]*(1-LPFgain);
	filteredARRAY[1] = filteredARRAY[0];
}

float calc_Angle(float ADC_value)
{
	float Angle = 0;
	Angle = 360 * ADC_value / 1024;
	return Angle;
}

void receiveAngles(char *str,float *receivedSetPoints)
{
	uint8_t i =0 ;
	char counter = 0 ;
	char strSetPoint[5]= {'\0'} ;
	char strSetPoint2[5]={'\0'} ;
	char strSetPoint3[5]={'\0'} ;
	float receivedAngles[3]={0} ;
		
	while (*str !=0x00)
	{
		if (*str != ',')
		{
			switch(counter)
			{
				case 0:
				strSetPoint[i]=*str;
				break ;
				case 1:
				strSetPoint2[i]=*str;
				break ;
				case 2:
				strSetPoint3[i]=*str;
				break ;
			}
			i++;
		}
		else
		{
			counter++;
			i=0 ;
		}
		str++ ;
	}
/*
	USART_Transmit_string(strSetPoint,0);	USART_Transmit_string("  ,  ",0) ;
	USART_Transmit_string(strSetPoint,0);   USART_Transmit_string("  ,  ",0) ;
	USART_Transmit_string(strSetPoint,0);   USART_Transmit_string("\r\n",0) ;*/
	
	receivedAngles[0] = atoi(strSetPoint) ;
	receivedAngles[1] = atoi(strSetPoint2) ;
	receivedAngles[2] = atoi(strSetPoint3) ;
	
	receivedSetPoints[0] = constrain(receivedAngles[0],0,90);
	receivedSetPoints[1] = constrain(receivedAngles[1],0,90);
	receivedSetPoints[2] = constrain(receivedAngles[2],0,90);
}

void cleanArr(char* StringPtr)
{
	while(*StringPtr != 0x00)
	{
		*StringPtr=0x00 ;
		StringPtr++;
	}
}

ISR(USART0_RX_vect)
{
	ATOMIC_BLOCK(ATOMIC_RESTORESTATE)
	{
		UarTemp=UDR0 ;
		static uint8_t i=0;
		if(UarTemp == 10)
		{
			
			receiveAngles(buffer,setPoint);
			i=0 ;
			cleanArr(buffer);
		}
		else
		{
			buffer[i]=UarTemp ;
			i++ ;
		}
	}
}



ISR(ADC_vect)
{
	uint8_t LMB = ADCL;
	uint16_t ADCvalue = ADCH <<8 | LMB;

	switch(ADMUX)
	{	
		case 0b01000000:
		ADMUX = 0b01000001;
		break;
			
		case 0b01000001:
		ADC_accu[0] +=ADCvalue ;
		counter[0]++ ;
		//USART_Transmit_int(ADCvalue,0)    ; USART_Transmit_string("   ,  ",0) ;
		ADMUX = 0b01000010;
		break;
		
		case 0b01000010:
		ADC_accu[1] +=ADCvalue ;
		counter[1]++ ;
		//USART_Transmit_int(ADCvalue,0)    ; USART_Transmit_string("   ,  ",0) ;
		ADMUX = 0b01000011;
		break;
		
		case 0b01000011:
		ADC_accu[2] +=ADCvalue ;
		counter[2]++ ;
		//USART_Transmit_int(ADCvalue,0)    ; USART_Transmit_string("\r\n",0) ;
		ADMUX = 0b01000001;
		break;
	}
	
	if (counter[0]>= 100)
	{
		ADC_accu[0] = (ADC_accu[0])/(counter[0]) ;
		LPfilter(ADC_accu[0],filter,0.65) ;
		Angle[0] = calc_Angle(filter[0]) ;
		
		ADC_accu[1] = (ADC_accu[1])/(counter[1]) ;
		LPfilter(ADC_accu[1],filter2,0.65) ;
		Angle[1] = calc_Angle(filter2[0]) ;
		
		ADC_accu[2] = (ADC_accu[2])/(counter[2]) ;
		LPfilter(ADC_accu[2],filter3,0.65) ;
		Angle[2] = calc_Angle(filter3[0]) ;
		
		/*USART_Transmit_int(setPoint[0],0);   USART_Transmit_string("   ,  ",0) ;
		USART_Transmit_int(setPoint[1],0);	 USART_Transmit_string("  , ",0) ;
		USART_Transmit_int(setPoint[2],0);   USART_Transmit_string("\r\n",0) ;*/
		
		/*USART_Transmit_int(filter[0],0)   ; USART_Transmit_string(" , ",0) ;
		USART_Transmit_int(filter2[0],0)  ; USART_Transmit_string(" , ",0) ;
		USART_Transmit_int(filter3[0],0)  ; USART_Transmit_string("----",0) ;*/
		
		USART_Transmit_int(Angle[0],0)    ; USART_Transmit_string(" , ",0) ;
		USART_Transmit_int(Angle[1],0)    ; USART_Transmit_string(" , ",0) ;
		//USART_Transmit_int(Angle[2],0)    ; USART_Transmit_string("----",0) ;
		USART_Transmit_int(Angle[2],0)    ; USART_Transmit_string(" \r\n ",0) ;
		
		/*USART_Transmit_int(PWMDuty[0],0)  ; USART_Transmit_string(" , ",0) ;
		USART_Transmit_int(PWMDuty[1],0)  ; USART_Transmit_string(" , ",0) ;
		USART_Transmit_int(PWMDuty[2],0)  ; USART_Transmit_string("\r\n",0) ;*/
		
		for (uint8_t i=0 ;i<3;i++)
		{
			ADC_accu[i] = 0;
			counter[i] = 0 ;
		}
		
	}
	ADC_startConversion();
}

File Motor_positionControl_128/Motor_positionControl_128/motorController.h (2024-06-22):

/*
 * IncFile1.h
 *
 * Created: 2014.07.03. 9:43:48
 *  Author: F
 */ 
/************************************************************************/
/* 
 ATMEGA128				  L298 (motor drive)
|-------------|			  |-----------|
|		 PC3  |___________| DIR1	  |
|		 PC4  |___________| DIR2      |
|		 PC5  |___________|	DIR3	  |
|			  |			  |			  |
|       PE3   |___________| PWM1	  |
|       PE4   |___________| PWM2      |
|       PE5	  |___________|	PWM3      |
|	  		  |			  |	  		  |
|-------------|			  |-----------|
                                                     */
/************************************************************************/
#ifndef MOTORCONTROLLER_H_
#define MOTORCONTROLLER_H_

//#include "lowPassFilter.h"
#include <stdlib.h>

#define constrain(amt,low,high) ((amt)<(low)?(low):((amt)>(high)?(high):(amt)))

#define Motor_controll_DDR	DDRC
#define Motor_controll_PORT	PORTC
#define Motor_controll_PIN	PINC


//#define STBY				PC4		//Standby
#define DIR1				PC2		//logic input Motor A
#define DIR2				PC3		//logic input Motor B
#define DIR3				PC4		//logic input Motor C

#define PWM1				PE3		//connected to ENA in L298
#define PWM2				PE4		//connected to ENB in L298
#define PWM3				PE5

#define PWMA_DDR			DDRE
#define PWMB_DDR			DDRE
#define PWMC_DDR			DDRE

#define CONSTRAIN			40

//#define PWM_LPF_GAIN		MOTOR_PWM_LPF_GAIN

void driveMotor(int motorA,int motorB,int motorC);
void init_MotorController(void);


void driveMotor(int motorA,int motorB,int motorC)
{
	if (motorA>0)
	{
		//positive direction
		Motor_controll_PORT |= 1<<DIR1;
		OCR3A = constrain(motorA,0,CONSTRAIN);
	}
	//If the PWM value is negative then turn the rotate to the opposite direction and use abs(PWM value)
	else if (motorA<=0)
	{
		//negative direction
		Motor_controll_PORT &= ~(1<<DIR1);
		OCR3A = constrain(abs(motorA),0,CONSTRAIN);
 	}
	if (motorB>0)
	{	
		//positive direction	
		Motor_controll_PORT |= 1<<DIR2;
		OCR3B = constrain(motorB,0,CONSTRAIN);
	}
// 	//If the PWM value is negative then turn the rotate to the opposite direction and use abs(PWM value) 
 	else if (motorB<=0)
	{
		//negative direction
		Motor_controll_PORT &= ~(1<<DIR2);
		OCR3B = constrain(abs(motorB),0,CONSTRAIN);
	}
	if (motorC>0)
	{
		//positive direction
		Motor_controll_PORT |= 1<<DIR3;
		OCR3C = constrain(motorC,0,CONSTRAIN);
	}
	//If the PWM value is negative then turn the rotate to the opposite direction and use abs(PWM value)
	else if (motorC<=0)
	{
		//negative direction
		Motor_controll_PORT &= ~(1<<DIR3);
		OCR3C = constrain(abs(motorC),0,CONSTRAIN);
	}	
}

void init_MotorController(void)
{
	PWMA_DDR |= 1<<PWM1;
	PWMB_DDR |= 1<<PWM2;
	PWMC_DDR |= 1<<PWM3;
	Motor_controll_DDR |= 1<<DIR1 | 1<<DIR2 | 1<<DIR3 ; 
}


#endif /* INCFILE1_H_ */

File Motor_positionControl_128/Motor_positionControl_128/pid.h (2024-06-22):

#ifndef PID_H_
#define PID_H_


typedef struct {
		float kp;
		float ki;
		float kd;

		float sp;
		float integral;
		float error_previous;

        unsigned int features;
		float intmax;
        float sat_max;
        float sat_min;
} PID_t;

typedef enum {
    PID_ENABLE_WINDUP   =   (1<<0),
    PID_DEBUG           =   (1<<1),
    PID_OUTPUT_SAT_MIN  =   (1<<2),
    PID_OUTPUT_SAT_MAX  =   (1<<3),
    PID_INPUT_HIST      =   (1<<4)
} PIDFeatures_t;

void    pid_init(PID_t *pid,float kp,  float ki, float kd);
void    pid_enable_feature(PID_t *pid,unsigned intfeature,float value);
void    pid_set(PID_t *pid, float sp);
float   pid_calculate(PID_t *pid,float val, float dt);
void	pid_update(PID_t *pid,float kp ,float ki, float kd,float sp );




#endif /* PID_H_ */
